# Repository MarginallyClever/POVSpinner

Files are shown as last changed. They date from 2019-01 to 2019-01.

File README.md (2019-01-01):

# POVSpinner

A spinning light animation that uses Persistence-of-vision.

Another great http://marginallyclever.com/ production.
Support us on Patreon!  https://www.patreon.com/imakerobots

## Demo

[start](https://www.instagram.com/p/Br9ADS2HSqk/)
[better](https://www.instagram.com/p/Br9ITGbnAZ6/)
[finished](https://www.instagram.com/p/BsEod8YnH0e/)
[But also](https://www.instagram.com/p/BsGuSJFnXem/)

## Parts (off the shelf)

1x [Slip ring](https://www.adafruit.com/product/736)
14x WS2811 LEDs @ 16.5mm spacing.
1x RUMBA board OR 1x Arduino Mega + RAMPs board
1x A4988 stepper driver
1x 12v2a power supply
8x M3x10 pan head phllips screws
1x 160mm GT2-6 timing belt
1x NEMA17 stepper motor (200-step-per-turn)
1x 20x27x4 bearing
2x M2x10 screwss
2x 2mm zap straps (zip ties)
A breadboard
Some wires

## Parts (manufactured)

LEDPlate (laser cut).  STL file has been included as an alternative.
MountingPlate (laser cut).  STL file has been included as an alternative.

All other STL files were 3D printed on a Prusai3Mk3 at default settings.
Most parts are a snug friction fit.

## Assembly

If this part is actually troubling you, open a ticket.

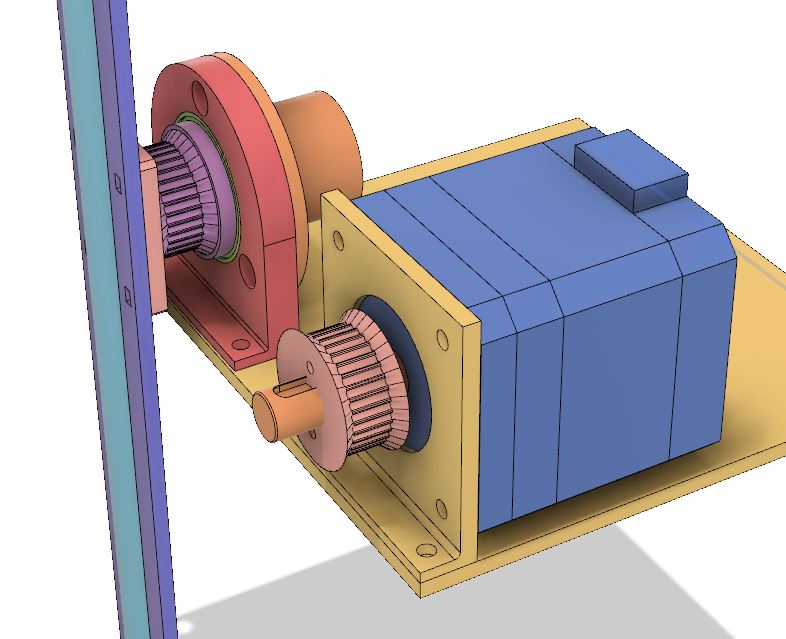
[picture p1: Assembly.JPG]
Assembly diagram


## Wiring

Pin 54 --> Slip ring red wire --> LED D0.
5v --> Slip ring white wire --> LED 5V.
GND --> Slip ring black wire --> LED G.

Stepper motor connected to X axis.
A4988 connected to X axis.

## Also

STLs available on [thingiverse](https://www.thingiverse.com/thing:3327441)
Code available on [github](https://github.com/MarginallyClever/POVSpinner)

## Thanks

Special thanks to [electronics_garage](https://www.instagram.com/electronics_garage/) for the suggestion.

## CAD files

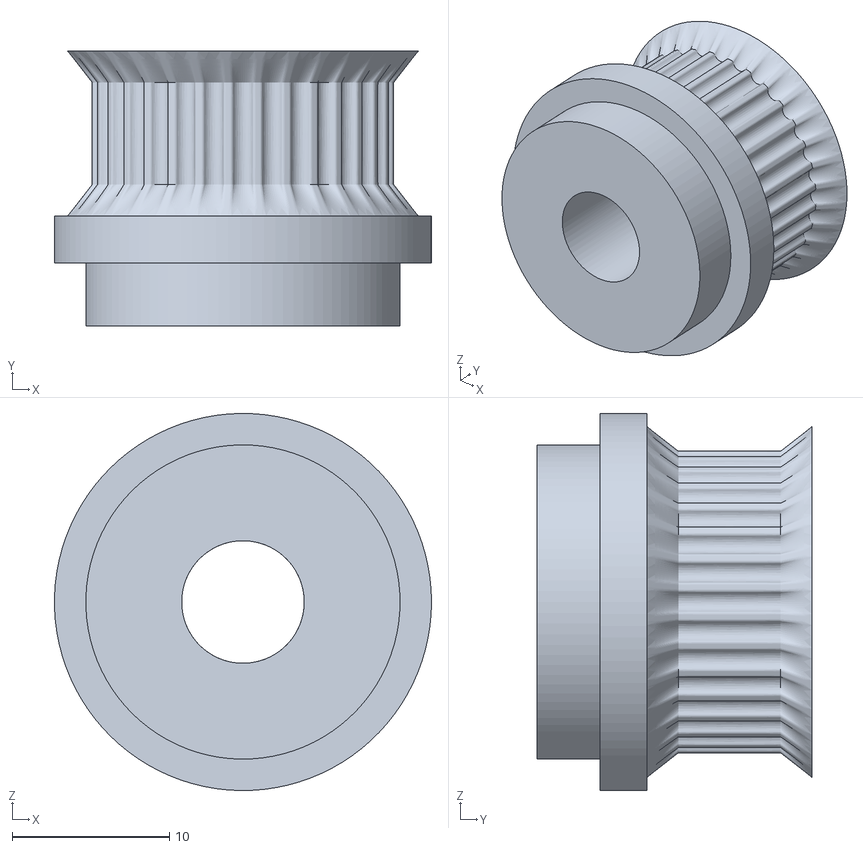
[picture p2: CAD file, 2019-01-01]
ring small part mount.stl
24.0 x 17.5 x 24.0

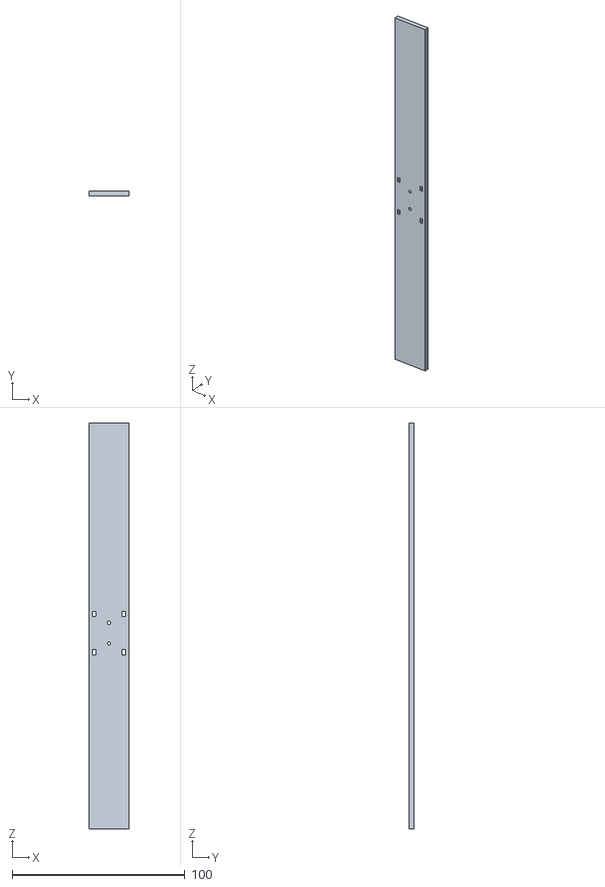
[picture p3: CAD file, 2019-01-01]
LEDBackPlate.stl
23.0 x 2.85 x 235.0

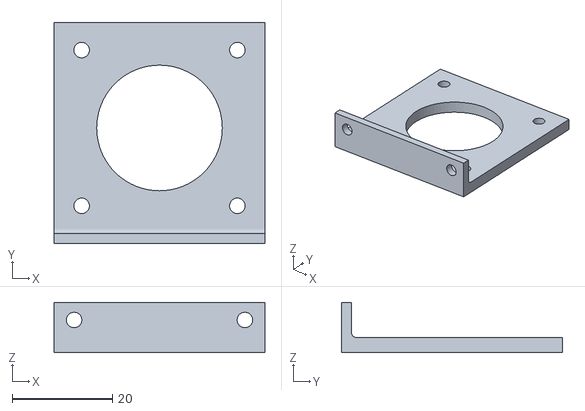
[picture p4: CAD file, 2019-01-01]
nema17 motor mount v1.stl
42.0 x 44.0 x 10.0

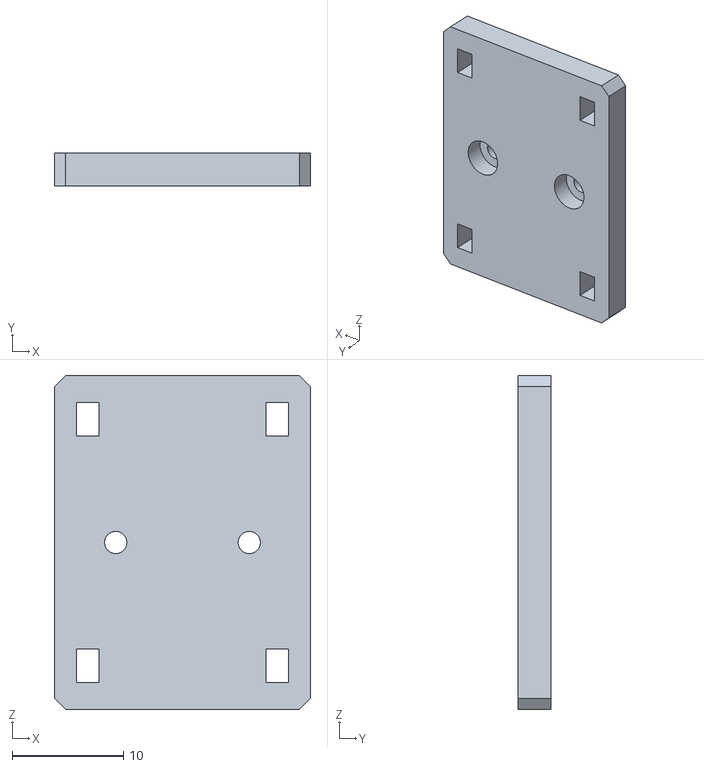
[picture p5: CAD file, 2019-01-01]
LEDPlate2RingSmallAdapter.stl
23.0 x 3.00 x 30.0

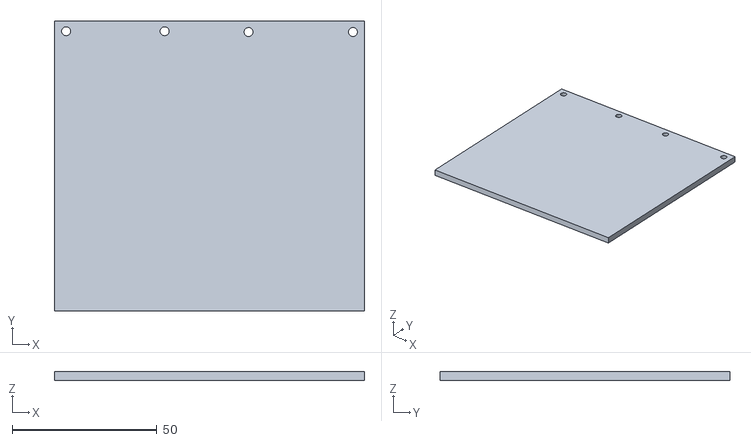
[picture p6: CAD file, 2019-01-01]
MountingPlate.stl
107.0 x 100.0 x 3.00

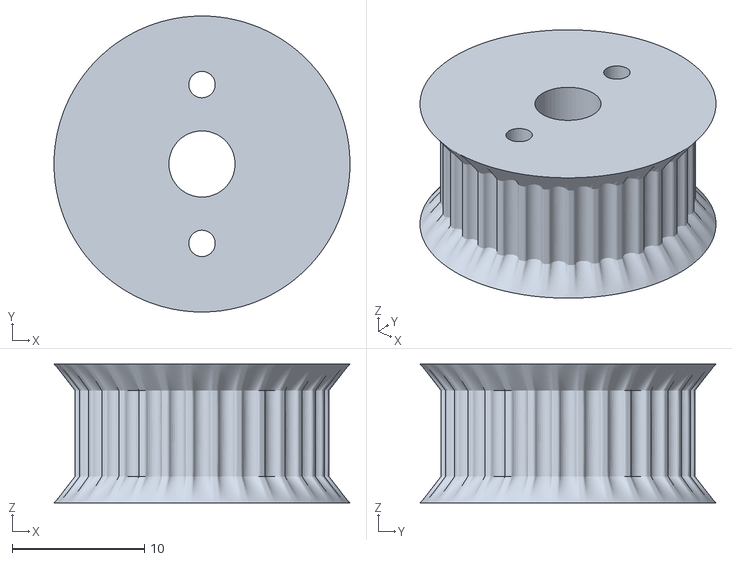
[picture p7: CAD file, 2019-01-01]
gear gt2-6-32.stl
22.4 x 22.4 x 10.5

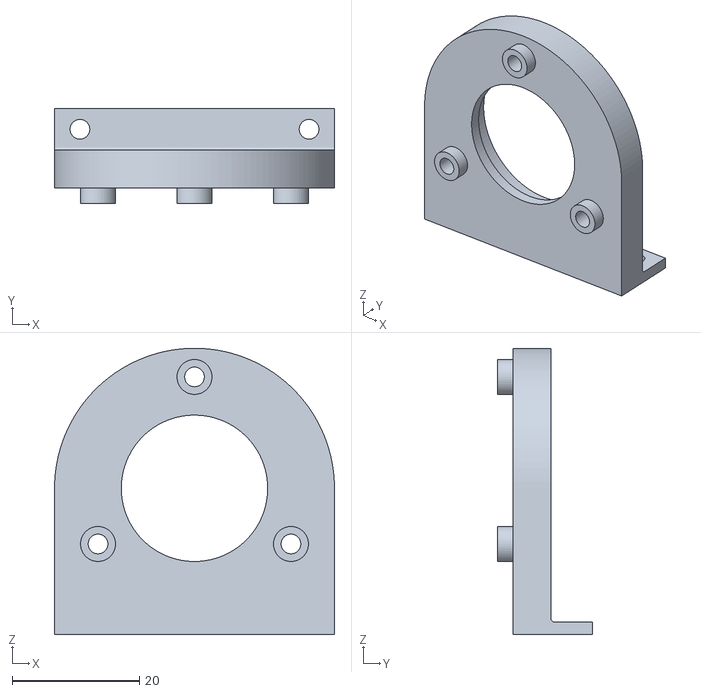
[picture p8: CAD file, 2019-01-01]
ring large part mount.stl
44.0 x 14.9 x 45.0

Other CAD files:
LEDBackPlate.dxf
MountingPlate.dxf

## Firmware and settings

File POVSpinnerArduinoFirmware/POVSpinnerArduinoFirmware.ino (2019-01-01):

// Persistence Of Vision spinning LED tutorial
// dan@marginallyclever.com (2019-01-01)
// https://github.com/MarginallyClever/POVSpinner

// supported boards
#define RUMBA 1
#define RAMPS 2

// your chosen board
//#define BOARD_TYPE RUMBA
//#define BOARD_TYPE RAMPS

// sanity check
#if !defined(BOARD_TYPE)
#error You must choose a board type!
#endif

// pin assignments
#if BOARD_TYPE == RAMPS
#define MOTOR_0_STEP_PIN              (54)
#define MOTOR_0_DIR_PIN               (55)
#define MOTOR_0_ENABLE_PIN            (38)
#define DATA_PIN 60  // Y_STEP_PIN
#endif

#if BOARD_TYPE == RUMBA
#define MOTOR_0_STEP_PIN              (17)
#define MOTOR_0_DIR_PIN               (16)
#define MOTOR_0_ENABLE_PIN            (48)
#define DATA_PIN 54  // Y_STEP_PIN
#endif


#define NUM_LEDS             14

#define STEPS_PER_TURN      200  // 1.8 degree stepper motor

// delay between steps when the machine starts moving.
#define START_DELAY        1200  // us
// delay between steps at top speed.
// the limiting factor is strip.show(), not the motor.
#define MIN_DELAY           500  // us

#define SPACING              16.5  // mm.  distance between lights

#define NUM_LIGHTS            7  // on each side
#define DEGREES_PER_TURN    360

#define GRID_SIZE             7  // bitmap grid is 7x7
#define GRID_SPACING (SPACING*2) // mm.  grid size.


#include <Adafruit_NeoPixel.h>
#ifdef __AVR__
  #include <avr/power.h>
#endif

// Parameter 1 = number of pixels in strip
// Parameter 2 = Arduino pin number (most are valid)
// Parameter 3 = pixel type flags, add together as needed:
//   NEO_KHZ800  800 KHz bitstream (most NeoPixel products w/WS2812 LEDs)
//   NEO_KHZ400  400 KHz (classic 'v1' (not v2) FLORA pixels, WS2811 drivers)
//   NEO_GRB     Pixels are wired for GRB bitstream (most NeoPixel products)
//   NEO_RGB     Pixels are wired for RGB bitstream (v1 FLORA pixels, not v2)
//   NEO_RGBW    Pixels are wired for RGBW bitstream (NeoPixel RGBW products)
Adafruit_NeoPixel strip = Adafruit_NeoPixel(NUM_LEDS, DATA_PIN, NEO_GRB + NEO_KHZ800);


// colors to display on the letters in the message.
#define COLOR_LIST_LENGTH   7
uint32_t color_list[] = {
  strip.Color(  0,  0,255),
  strip.Color(  0,255,  0),
  strip.Color(255,  0,  0),
  strip.Color(  0,255,255),
  strip.Color(255,255,  0),
  strip.Color(255,  0,255),
  strip.Color(255,255,255),
};

  
///////////// LETTER BITMAPS ///////////////////
char grid_h[] = {  // GRID_SIZE*GRID_SIZE
0,0,0,0,0,0,0,
0,1,0,0,0,1,0,
0,1,0,0,0,1,0,
0,1,1,1,1,1,0,
0,1,0,0,0,1,0,
0,1,0,0,0,1,0,
0,0,0,0,0,0,0,
};

char grid_a[] = {  // GRID_SIZE*GRID_SIZE
0,0,0,0,0,0,0,
0,0,1,1,1,0,0,
0,1,0,0,0,1,0,
0,1,1,1,1,1,0,
0,1,0,0,0,1,0,
0,1,0,0,0,1,0,
0,0,0,0,0,0,0,
};

char grid_p[] = {  // GRID_SIZE*GRID_SIZE
0,0,0,0,0,0,0,
0,1,1,1,1,0,0,
0,1,0,0,0,1,0,
0,1,1,1,1,0,0,
0,1,0,0,0,0,0,
0,1,0,0,0,0,0,
0,0,0,0,0,0,0,
};

char grid_y[] = {  // GRID_SIZE*GRID_SIZE
0,0,0,0,0,0,0,
0,1,0,0,0,1,0,
0,1,0,0,0,1,0,
0,0,1,1,1,0,0,
0,0,0,1,0,0,0,
0,0,0,1,0,0,0,
0,0,0,0,0,0,0,
};

char grid__[] = {  // GRID_SIZE*GRID_SIZE
0,0,0,0,0,0,0,
0,0,0,0,0,0,0,
0,0,0,0,0,0,0,
0,0,0,0,0,0,0,
0,0,0,0,0,0,0,
0,0,0,0,0,0,0,
0,0,0,0,0,0,0,
};

char grid_n[] = {  // GRID_SIZE*GRID_SIZE
0,0,0,0,0,0,0,
0,1,0,0,0,1,0,
0,1,1,0,0,1,0,
0,1,0,1,0,1,0,
0,1,0,0,1,1,0,
0,1,0,0,0,1,0,
0,0,0,0,0,0,0,
};

char grid_e[] = {  // GRID_SIZE*GRID_SIZE
0,0,0,0,0,0,0,
0,1,1,1,1,1,0,
0,1,0,0,0,0,0,
0,1,1,1,0,0,0,
0,1,0,0,0,0,0,
0,1,1,1,1,1,0,
0,0,0,0,0,0,0,
};

char grid_w[] = {  // GRID_SIZE*GRID_SIZE
0,0,0,0,0,0,0,
0,1,0,0,0,1,0,
0,1,0,0,0,1,0,
0,1,0,1,0,1,0,
0,1,0,1,0,1,0,
0,0,1,0,1,0,0,
0,0,0,0,0,0,0,
};

char grid_r[] = {  // GRID_SIZE*GRID_SIZE
0,0,0,0,0,0,0,
0,1,1,1,1,0,0,
0,1,0,0,0,1,0,
0,1,1,1,1,0,0,
0,1,0,0,1,0,0,
0,1,0,0,0,1,0,
0,0,0,0,0,0,0,
};

char grid_2[] = {  // GRID_SIZE*GRID_SIZE
0,0,0,0,0,0,0,
0,0,1,1,1,0,0,
0,0,0,0,1,0,0,
0,0,1,1,1,0,0,
0,0,1,0,0,0,0,
0,0,1,1,1,0,0,
0,0,0,0,0,0,0,
};

char grid_0[] = {  // GRID_SIZE*GRID_SIZE
0,0,0,0,0,0,0,
0,0,1,1,1,0,0,
0,0,1,0,1,0,0,
0,0,1,0,1,0,0,
0,0,1,0,1,0,0,
0,0,1,1,1,0,0,
0,0,0,0,0,0,0,
};

char grid_1[] = {  // GRID_SIZE*GRID_SIZE
0,0,0,0,0,0,0,
0,0,0,1,0,0,0,
0,0,0,1,0,0,0,
0,0,0,1,0,0,0,
0,0,0,1,0,0,0,
0,0,0,1,0,0,0,
0,0,0,0,0,0,0,
};

char grid_9[] = {  // GRID_SIZE*GRID_SIZE
0,0,0,0,0,0,0,
0,0,1,1,1,0,0,
0,0,1,0,1,0,0,
0,0,1,1,1,0,0,
0,0,0,0,1,0,0,
0,0,1,1,1,0,0,
0,0,0,0,0,0,0,
};


#define GRID_LIST_LENGTH 20  // length of the message
// A list of pointers to each bitmap.
char *grid_list[] {
  grid_h,
  grid_a,
  grid_p,
  grid_p,
  grid_y,
  grid__,
  grid_n,
  grid_e,
  grid_w,
  grid__,
  grid_y,
  grid_e,
  grid_a,
  grid_r,
  grid__,
  grid_2,
  grid_0,
  grid_1,
  grid_9,
  grid__,
};

// which letter is being displayed now?
int grid_list_index;
// a pointer to the current bitmap.
char *grid;


// how long to delay between each step of the motor.
// this is used to accelerate at the start and achieve a higher top speed.
int newWait=START_DELAY;


// the bitmap floats invisibly in space.  This tool remembers where each bitmap
// pixel is floating
struct GridCell {
  float x,y;
  int index;
};
GridCell cells[GRID_SIZE*GRID_SIZE];

// a map between the angle-distance of a light and the x/y position of each bitmap pixel.
int angleLightCell[DEGREES_PER_TURN * NUM_LIGHTS];



void setup() {
  pinMode(MOTOR_0_STEP_PIN  ,OUTPUT);
  pinMode(MOTOR_0_DIR_PIN   ,OUTPUT);
  pinMode(MOTOR_0_ENABLE_PIN,OUTPUT);

  digitalWrite(MOTOR_0_DIR_PIN,HIGH);
  
  strip.begin();
  strip.show(); // Initialize all pixels to 'off'

  grid_list_index=0;
  grid = grid_list[0];

  Serial.begin(57600);
  Serial.println("Calculating grid cells...");

  for(int y=0;y<GRID_SIZE;++y) {
    for(int x=0;x<GRID_SIZE;++x) {
      int index=y*GRID_SIZE+x;
      cells[index].index=index;
      
      float x0=((float)x-GRID_SIZE/2)*GRID_SPACING;
      float y0=((float)y-GRID_SIZE/2)*GRID_SPACING;
      cells[index].x=x0;
      cells[index].y=y0;
    }
  }
  
  Serial.println("Calculating angle/light/cell relationships...");
  for(int a=0;a<DEGREES_PER_TURN;++a) {
    float c = cos(radians(a));
    float s = sin(radians(a));
    for(int i=0;i<NUM_LIGHTS;++i) {
      // find the x,y of the current light
      float x = (float)NUM_LIGHTS/2.0 + -s*((float)i*SPACING+SPACING/2);
      float y = (float)NUM_LIGHTS/2.0 + c*((float)i*SPACING+SPACING/2);
      // match to the nearest grid square
      int nearest=-1;
      float nearestDistance=SPACING*SPACING*NUM_LIGHTS;
      
      for(int j=0;j<GRID_SIZE*GRID_SIZE;++j) {
        float dx = cells[j].x-x;
        float dy = cells[j].y-y;
        float distance = dx*dx+dy*dy; 
        if( nearestDistance > distance ) {
          nearestDistance = distance;
          nearest=j;
        }
      }
      angleLightCell[a*NUM_LIGHTS+i]=nearest;
    }  
  }
  Serial.println("------- READY -------");
}


void loop() {
  uint16_t i, j=0, dir=1,s=0,t2=0;
  int angle, cellID;
  int color_list_index=0;

  uint32_t c3=color_list[color_list_index];
  const float aInc = 360.0/(float)STEPS_PER_TURN;
  float aSum=0;
  int *offset;
  int *offset2;
  unsigned long tEnd;
  
  long nextLetterTime=millis()+500;

  // adjust brightness to taste.
  strip.setBrightness(64);
  
  do {
    tEnd = micros() + newWait;
    digitalWrite(MOTOR_0_STEP_PIN,LOW);

    // count rotation steps
    s++;
    aSum+=aInc;
    if(s>=STEPS_PER_TURN) {
      s=0;
      aSum=0;
    }
    angle = aSum;

    // use the lookup table to find which grid cell is closest to each light.
    // then use the grid cell to find the color of the current letter bitmap.
    offset  = angleLightCell + ((angle    )    )*NUM_LIGHTS;
    offset2 = angleLightCell + ((angle+180)%360)*NUM_LIGHTS;
    for(i=0; i<NUM_LIGHTS; i++) {
      strip.setPixelColor(NUM_LIGHTS+i  , grid[offset [i]]*c3);  // light one half of the strip
      strip.setPixelColor(NUM_LIGHTS-1-i, grid[offset2[i]]*c3);  // light the other half
    }
    strip.show();

    // wait a bit
    while(micros()<tEnd);
    
    // step the motor
    digitalWrite(MOTOR_0_STEP_PIN,HIGH);

    // accelerate
    if(newWait>MIN_DELAY) {
      if(t2++>2) {  // >2 controls the acceleration. >10 would be slower.
        newWait--;
        t2=0;
      }
    }

    // change to the next letter and next color?
    if(millis()>nextLetterTime) {
      nextLetterTime=millis()+400;

      grid_list_index = (grid_list_index+1)%GRID_LIST_LENGTH;
      grid = grid_list[grid_list_index];

      color_list_index = (color_list_index+1)%COLOR_LIST_LENGTH;
      c3=color_list[color_list_index];
    }
  } while(1);
}
